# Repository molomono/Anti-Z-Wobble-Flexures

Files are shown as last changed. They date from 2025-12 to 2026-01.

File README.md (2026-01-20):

# Anti-Z-Wobble Flexures
Low cost SOTA performance 3d printable flexure based drop-in substitute for Oldham couplings.   
Onshape project focussing on solving z-axis misalignment and wobble induced printing artifacts using flexures.

---
Z-wobble in 3D printing is a mechanical issue where the Z-axis (vertical) movement isn't perfectly straight, 
causing the nozzle to shift slightly sideways, resulting in visible, repeating horizontal lines or ripples 
(Z-banding) on the print's surface. It's a hardware problem, often from bent lead screws, misaligned couplers,
and leads to inconsistent layer stacking. 

The approach to solving z-wobble and related artifacts is by releasing the x and y degrees of freedom at 
the interface between the T8-nut and the printer bed. (Same as any anti-wobble nut, oldham couplings, WobbleX) 
These DOFs are over-constrained by the linear rails AND the threaded rod. 
This project utilizes [Flexures](https://en.wikipedia.org/wiki/Flexure) to achieve this constraint relaxation. 
See [FACT](https://en.wikipedia.org/wiki/Freedom_and_constraint_topologies) for more info on design considerations.

---
## Quick Overview

Two primary designs, sharing common metrics for performance.   
	- High relative stiffness between z and x-y axes,    
		- High stiffness in z axis. Flexure must easily support the bed under fast accelrations.   
		- Low stiffness in x y axes.   
	- High resistance to tortion around z.   
	- Parametric Design So the dimensions of the model can easily be changed to better fit the users requirements. (see Onshape Workflow below)

Main benefits:   
	- Fixes minor misalignments, (releasing overconstrained Z-motion system)   
	- Flexure, thus no friction motion, therefore low hysteresis. (State of the Art performance for T8 threaded z-axis printers)   
	- Exceptionally low cost, (3D printed designs, practically free except for a few M2.5/M3 screws)   

Main downside:
	- Use in heated environments will require apropriate choice of material.

---

| Design | Key property | Onshape Link |
| :--- | :--- | :--- |
| **Design A V2: [Parallelogram]** | [Low x,y stiffness] | [Open Live Model 🔗](https://cad.onshape.com/documents/e9f5f3ec017cd79d059d23d6/w/ac5a599820a5beecc4798aae/e/dd3290a3d811bc061c931160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) |
| **Design A V3: [Parallelogram]** | [Stiffer Z DoFs] | [Open Live Model 🔗](https://cad.onshape.com/documents/0bdb8cc5919d48aaf7c68062/w/57636940a288332a187afe87/e/9ee4d49a4399172ee17dd28a) |
| **Design B: [Planar]** | [Flat profile] | [Open Live Model 🔗](https://cad.onshape.com/documents/95f8fcc605a67b3147b08d67/w/e3557ddfdb1231eb4b031d51/e/2aff83f88191c0ca42ad76a6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) |

---

## 1. Design A: [Parallelogram]
[V3 is the Recommended Design, well suited for 3d printing and dimensions are similar to oldham coupling.]

<p align="center">
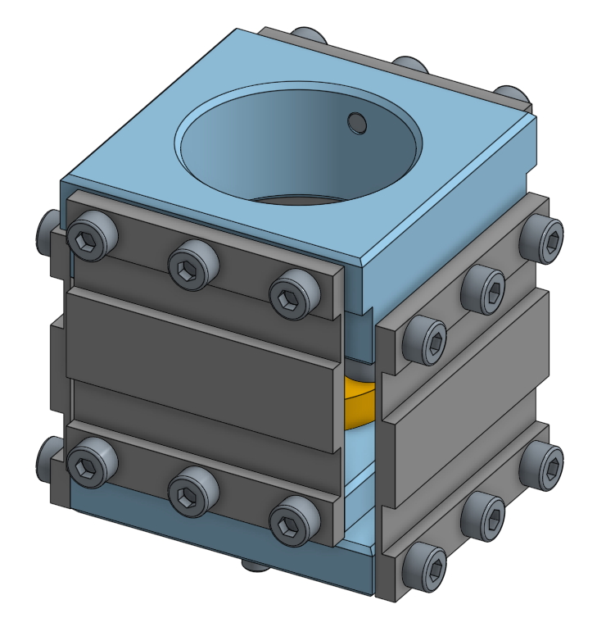
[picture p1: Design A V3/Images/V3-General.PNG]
  
</p>

<table border="0" align="center">
  <tr>
    <td>
      <p align="center"><b>Design A: Standard</b></p>
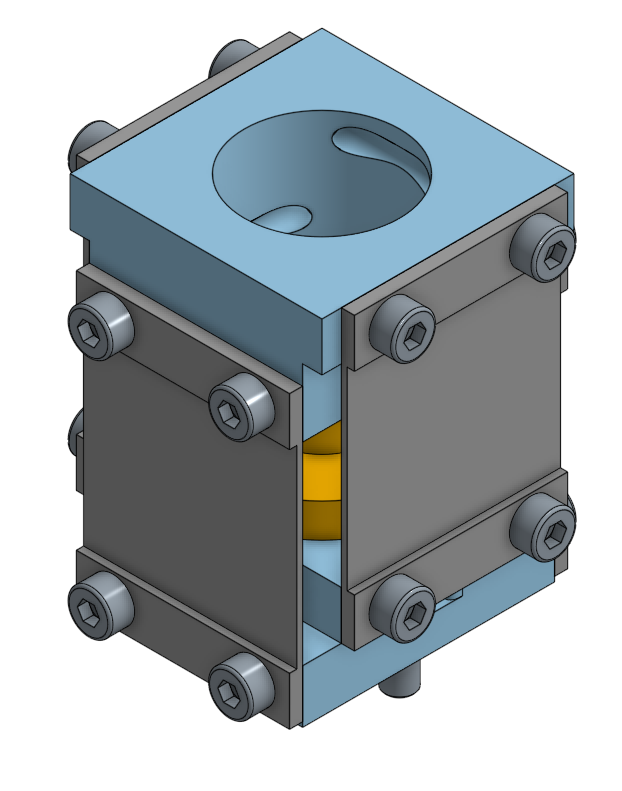
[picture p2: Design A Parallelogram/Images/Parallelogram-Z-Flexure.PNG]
      
    </td>
    <td>
      <p align="center"><b>Design A: Reinforced Leaf Springs</b></p>
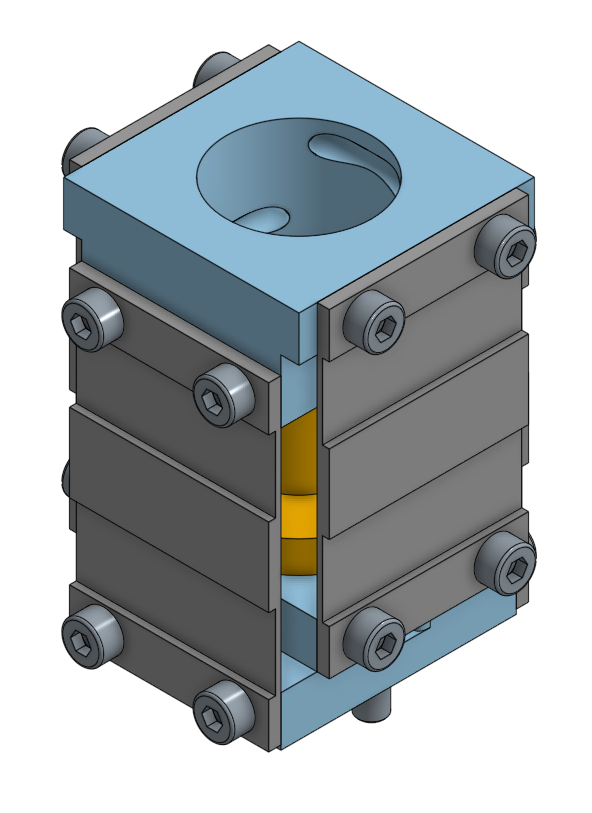
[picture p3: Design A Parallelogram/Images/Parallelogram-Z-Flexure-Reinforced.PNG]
      
    </td>
  </tr>
</table>

### Key Specifications
* **Standard Dimensions:** 28.7x28.7x37.5mm (without bolts)
* **Reinforced Dimensions:** 28.7x28.7x42.833mm (without bolts) (reinforced leaf spring version)
* **V3 Dimensions:** 38.8x38.8x39.0mm (without bolts) (V3 reinforced leaf spring version)
* **Hardware Required:** BOM: M3x8mm 8 times, M2.5x8mm 16 times (V3 uses 24), Threaded T8-Nut
* **Main Features:**  
	**Pros**: Easily achieves low x-y stiffness while maintaining high stiffness in other DOFs. 
		Easier printing, and stiffness tuning than design B.   
	**Cons**: Z-deflection becomes relational to x-y deflections (see figure) & "Tricky" assembly

<p align="center">
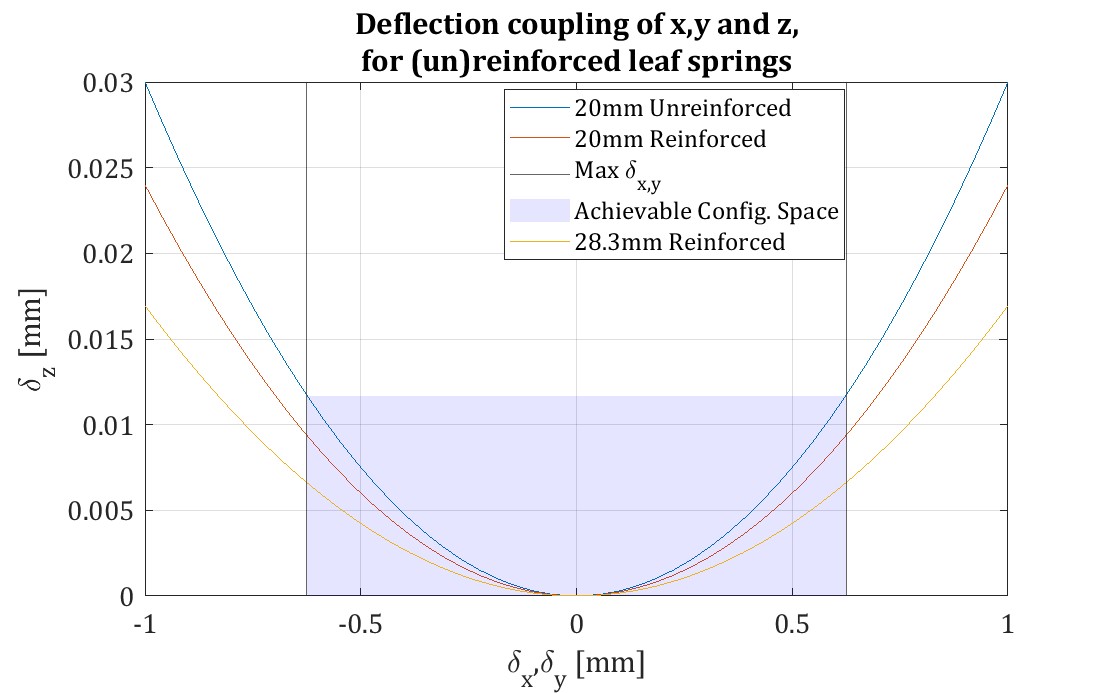
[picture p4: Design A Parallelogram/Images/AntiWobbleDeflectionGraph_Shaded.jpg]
Deflection in Z as product of deflection in x,y
  
</p>

<table border="0" align="center">
  <tr>
    <td>
      <p align="center"><b>Design A: Standard</b></p>
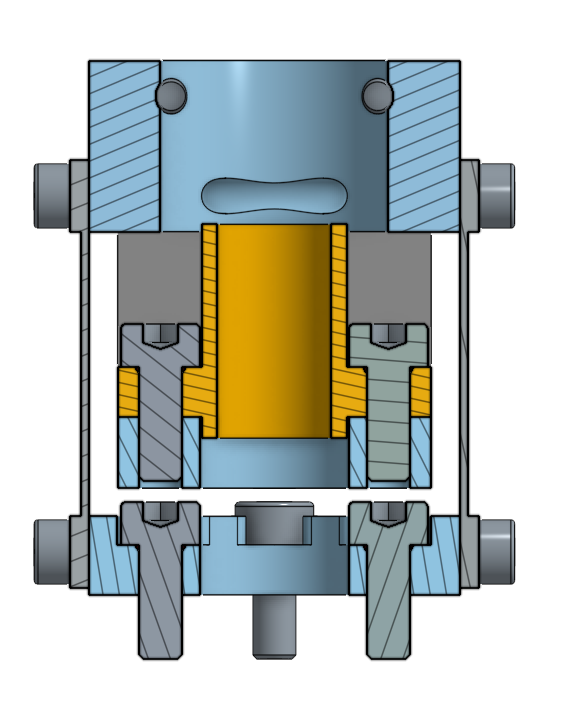
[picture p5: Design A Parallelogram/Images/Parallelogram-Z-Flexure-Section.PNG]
      
    </td>
    <td>
      <p align="center"><b>Design A: Reinforced Leaf Springs</b></p>
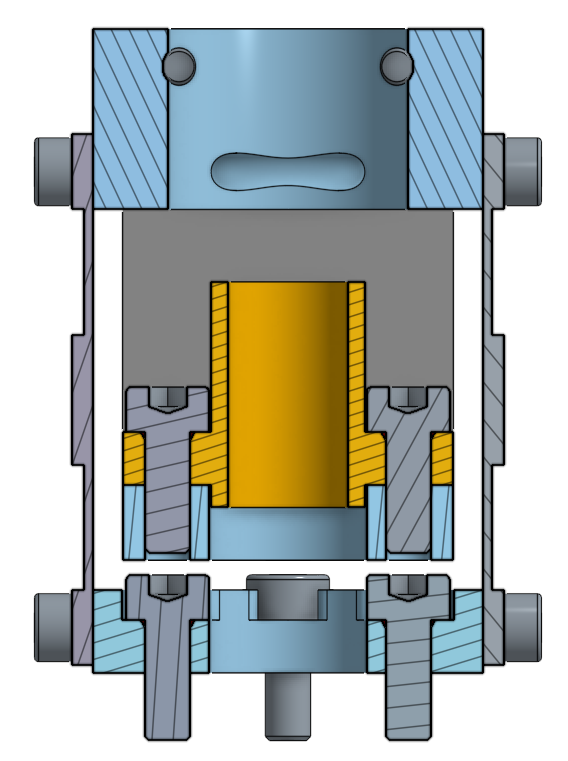
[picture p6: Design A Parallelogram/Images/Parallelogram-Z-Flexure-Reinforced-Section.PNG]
      
    </td>
  </tr>
</table>

**Note: Highly recommended to use Torx for any bolts below M3 because hex-bolts start stripping easily.**

---

## 2. Design B: [Planar]
[Experimentation with linear planar motion stages. This design works but is more difficult to print, but the design is well suited to be adapted for a CNC based solution can easily be machined.]

<p align="center">
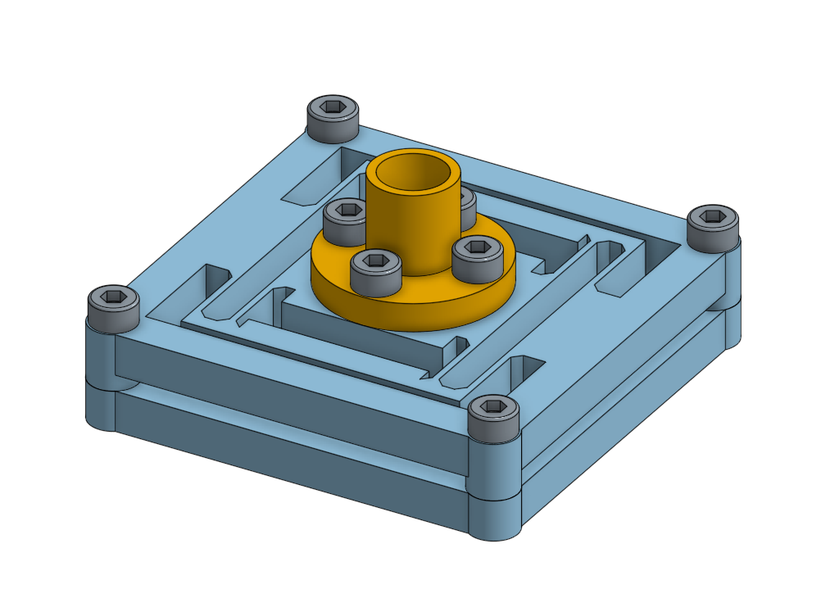
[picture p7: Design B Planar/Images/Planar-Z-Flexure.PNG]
  
</p>

### Key Specifications
* **Dimensions:** 52x52x12.5mm (without bolts)  
* **Hardware Required:** M3x8mm 8 times, M3x12mm 4 times, Threaded T8-Nut   
* **Main Features:**   
  	**Pros**: Very simple, symetric design, design structure well suited CNC machining.  
	**Cons**: Lower relative stiffness, akward shape, harder to print.  

<p align="center">
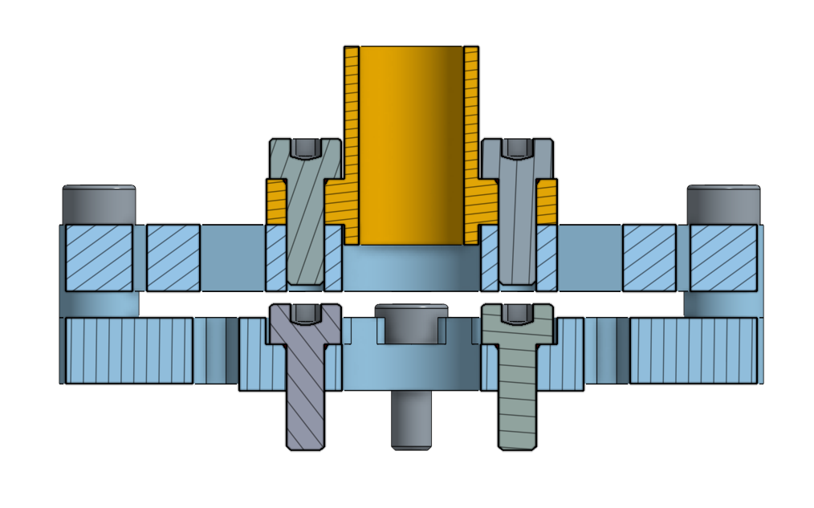
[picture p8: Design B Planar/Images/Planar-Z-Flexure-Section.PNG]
  
</p>

---

## Notes on print-settings
### Design A:
* I used PLA but PLA-CF/-GF might improve performance due to the print orietnation of the springs.
* Leaf springs must be printed flat with the reinforcements pointed up. Make sure that the unreinforced part of the springs is 100% considered bottom/top shell.
* Using rectilinear infill makes for good internal reinforcement structure. 30% is sufficient.
* Use 3-4 perimeter walls and 30% infill on the other printed boddies.
* Over-extruding the first layer is fine for functionality of this part, underextruding WILL cause issues.

### Design B:
* Make sure the seams do not align near the connection point between spring and body.
* Make sure the nozzle diameter ensures there are at least 2 walls in each spring.
* If the above requirements aren't met the springs can disconnect from the body.

---

### Onshape Workflow
To modify this design:
1. Open [Parallelogram Design](https://cad.onshape.com/documents/e9f5f3ec017cd79d059d23d6/w/ac5a599820a5beecc4798aae/e/dd3290a3d811bc061c931160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) or [Planar Design](https://cad.onshape.com/documents/95f8fcc605a67b3147b08d67/w/e3557ddfdb1231eb4b031d51/e/2aff83f88191c0ca42ad76a6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).
2. Click **"Make a Copy"** (requires a free Onshape account) to edit.
3. The variable table can be opened on the right from which dimensions of the model can be altered to better suit your needs.

---

## ⚖️ License

This project is licensed under the **Open Community License (OCL)**.
[View the full OCL terms here](https://github.com/OpenCommunityLicence/OpenCommunityLicence)

---

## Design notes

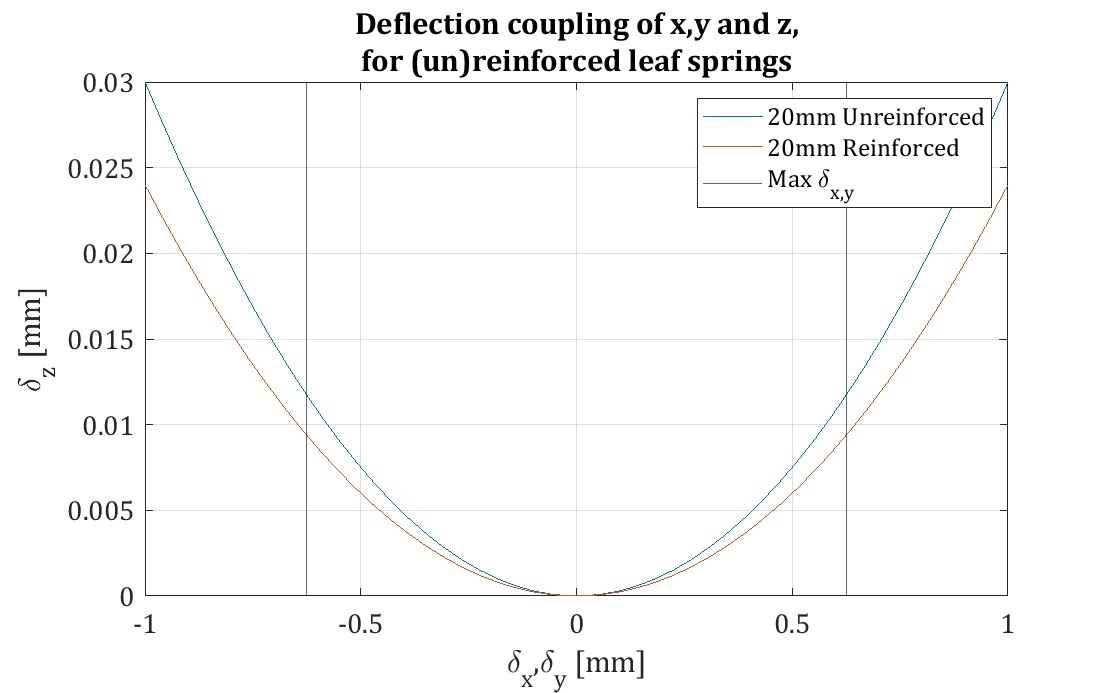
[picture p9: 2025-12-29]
Design A Parallelogram/Images/AntiWobbleDeflectionGraph.jpg

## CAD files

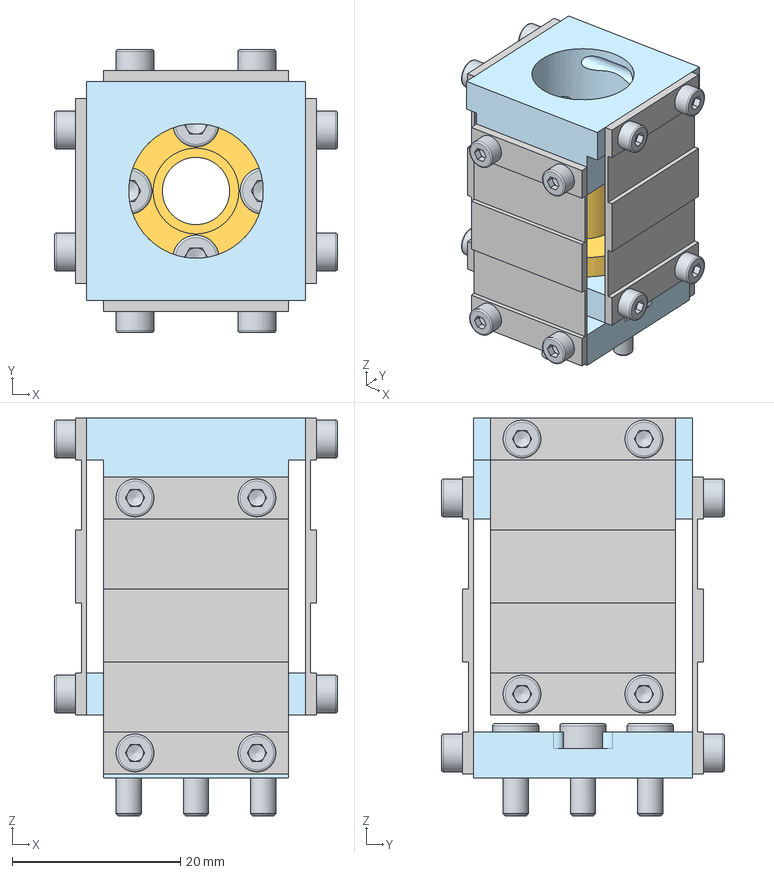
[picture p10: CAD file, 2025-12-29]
Design A Parallelogram/3D/CAD/Anti-Wobble-Flexure-M2.5 Reinforced.step
33.7 x 33.7 x 47.3 mm
Carriage Y
Hex socket head cap screw M3x0.50 x 8 x 8
Leaf1 x 4
Hex socket head cap screw M2.5x0.45 x 8 x 16
T8-Nut
Intermediate
Carriage X

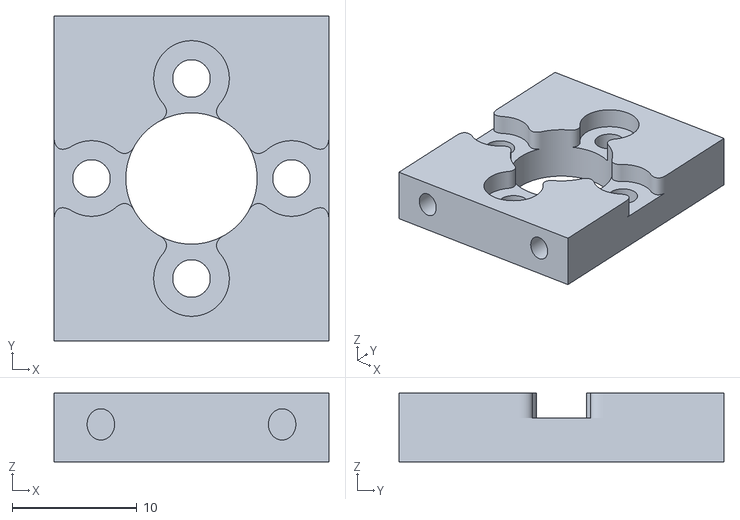
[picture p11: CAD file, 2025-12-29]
Design A Parallelogram/3D/WobbleFlexureM2.5 V2 - Carriage Bed.stl
22.0 x 26.0 x 5.50

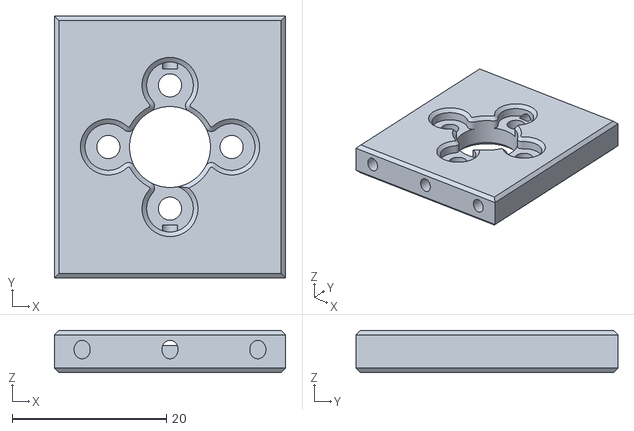
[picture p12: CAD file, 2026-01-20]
Design A V3/3D/WobbleFlexureM2.5 V3 - Carriage X.stl
30.0 x 34.0 x 5.50

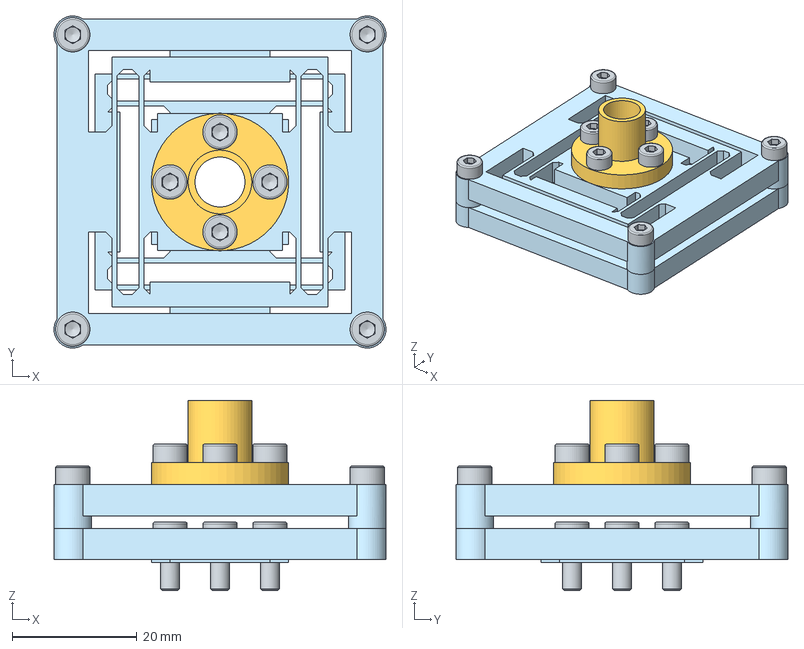
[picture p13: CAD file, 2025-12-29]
Design B Planar/3D/CAD/Anti-Wobble-Flexure-Planar.step
53.2 x 53.2 x 30.5 mm
Hex socket head cap screw M3x0.50 x 12 x 4
Carriage Top
Hex socket head cap screw M3x0.50 x 8 x 8
T8-Nut
Carriage Bottom

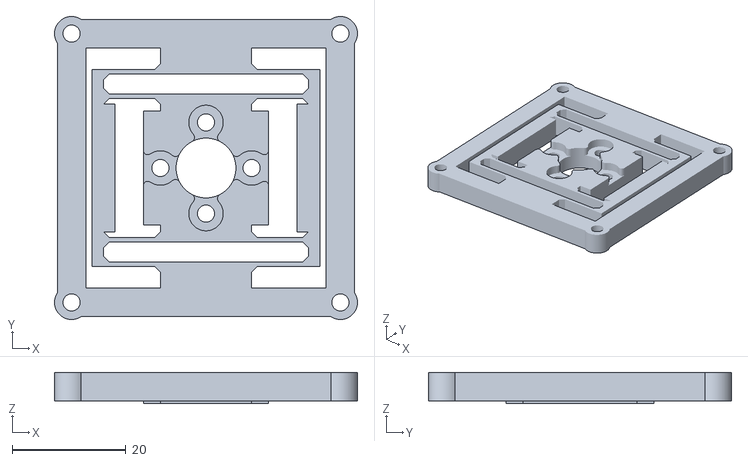
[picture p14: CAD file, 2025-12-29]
Design B Planar/3D/Wobble_Flexure_Planar - Carriage Bottom.stl
53.2 x 53.2 x 5.50

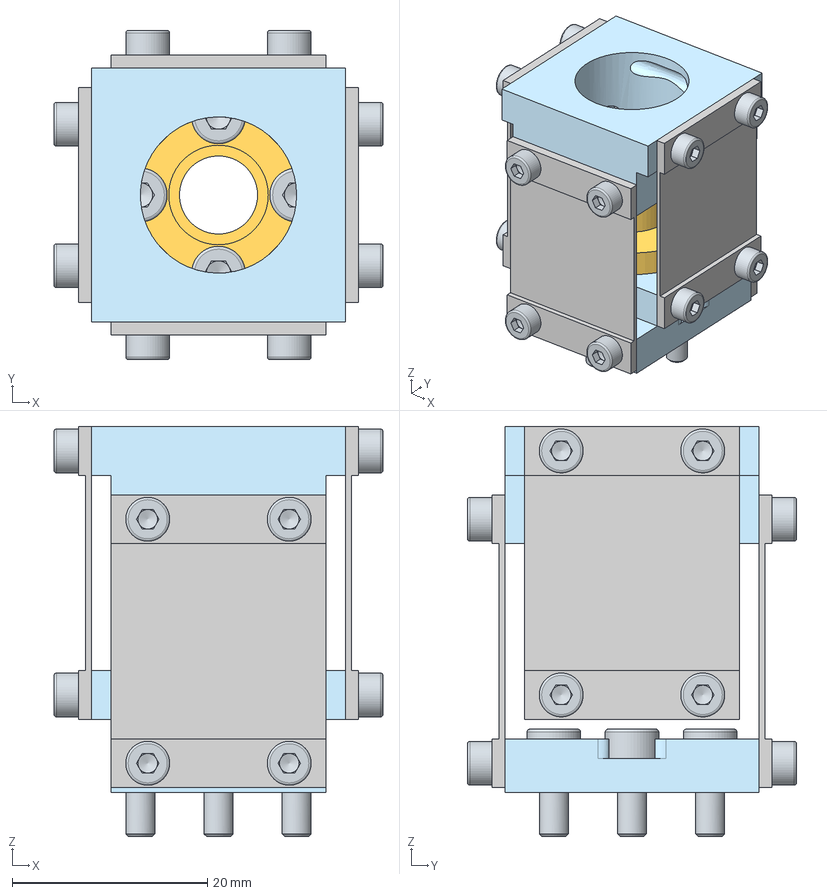
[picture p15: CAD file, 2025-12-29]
Design A Parallelogram/3D/CAD/Anti-Wobble-Flexure-M2.5 Short.step
33.7 x 33.7 x 42.0 mm
Carriage Y
Hex socket head cap screw M3x0.50 x 8 x 8
Leaf_Small x 4
Hex socket head cap screw M2.5x0.45 x 8 x 16
T8-Nut
Intermediate
Carriage X

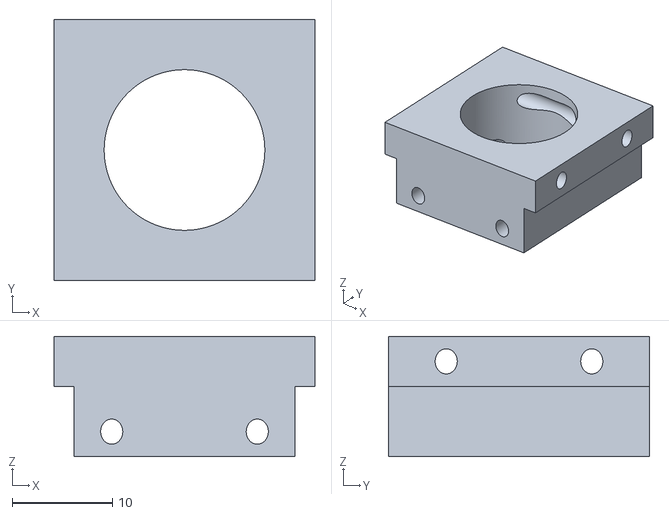
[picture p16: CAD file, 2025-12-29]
Design A Parallelogram/3D/WobbleFlexureM2.5 V2 - Intermediate.stl
26.0 x 26.0 x 12.0

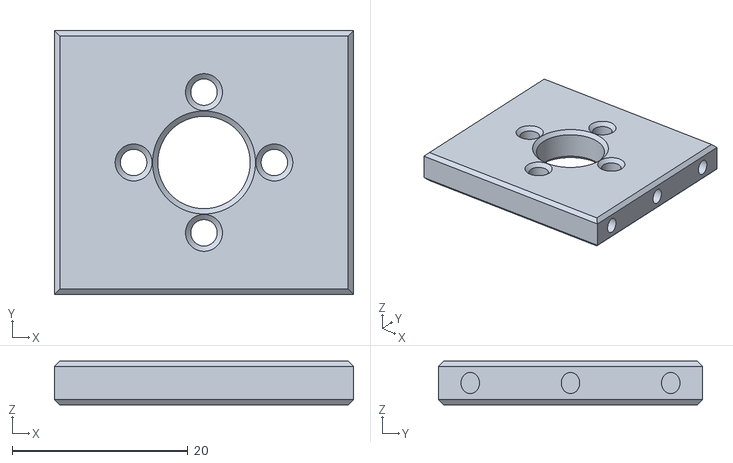
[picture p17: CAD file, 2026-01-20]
Design A V3/3D/WobbleFlexureM2.5 V3 - Carriage Y.stl
34.0 x 30.0 x 5.00

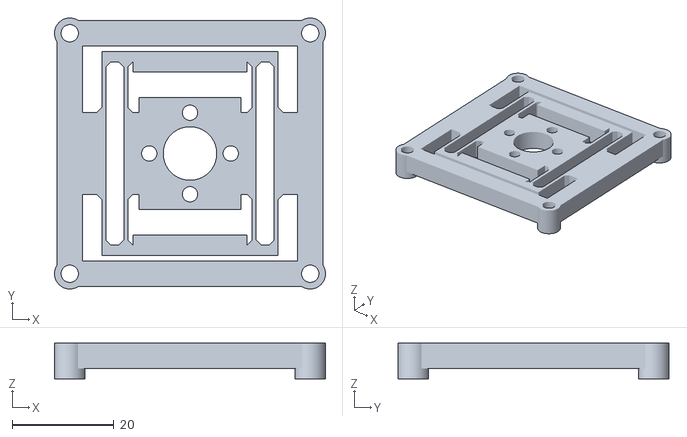
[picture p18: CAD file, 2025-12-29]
Design B Planar/3D/Wobble_Flexure_Planar - Carriage Top.stl
53.2 x 53.2 x 7.00

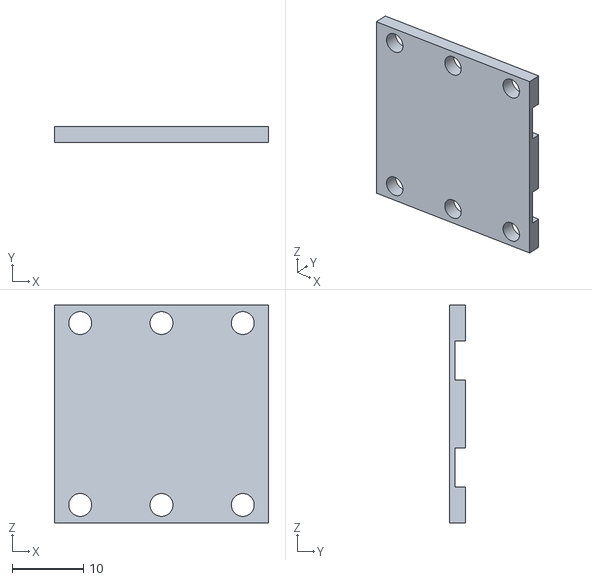
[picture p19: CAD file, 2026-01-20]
Design A V3/3D/WobbleFlexureM2.5 V3 - Leaf1 Reinforced.stl
30.0 x 2.25 x 30.5

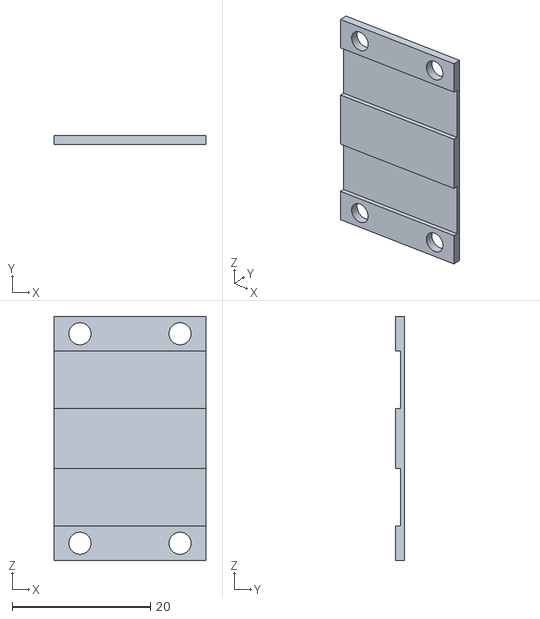
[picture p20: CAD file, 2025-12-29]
Design A Parallelogram/3D/WobbleFlexureM2.5 V2 - Leaf_Reinforced.stl
22.0 x 1.35 x 35.3

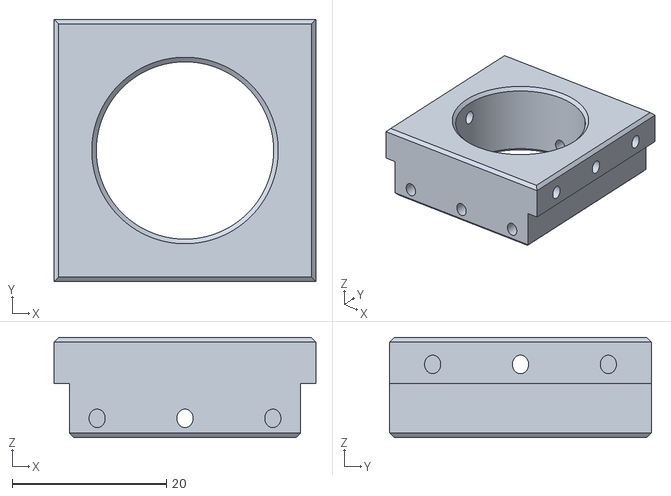
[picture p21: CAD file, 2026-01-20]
Design A V3/3D/WobbleFlexureM2.5 V3 - Intermediate.stl
34.0 x 34.0 x 13.0

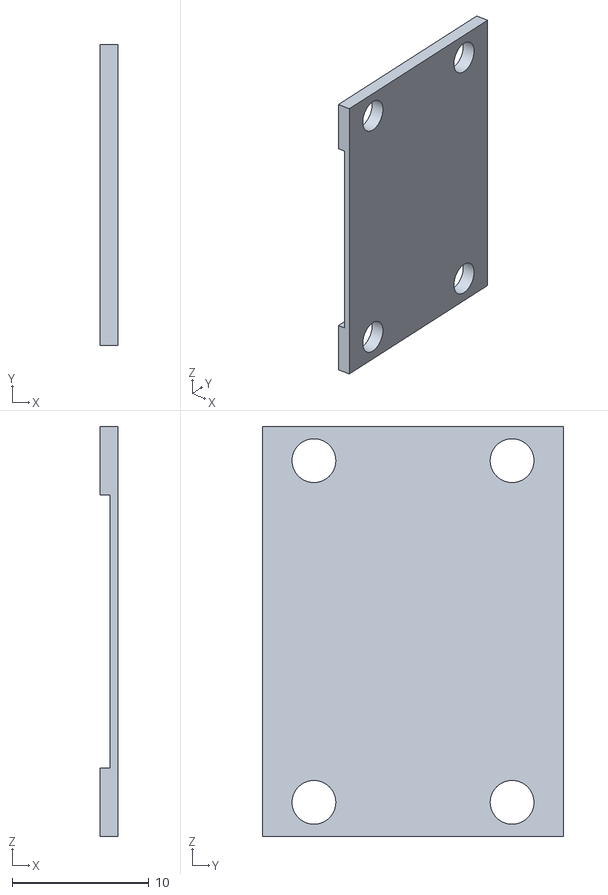
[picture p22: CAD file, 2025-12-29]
Design A Parallelogram/3D/WobbleFlexureM2.5 V2 - Leaf_Small.stl
1.35 x 22.0 x 30.0

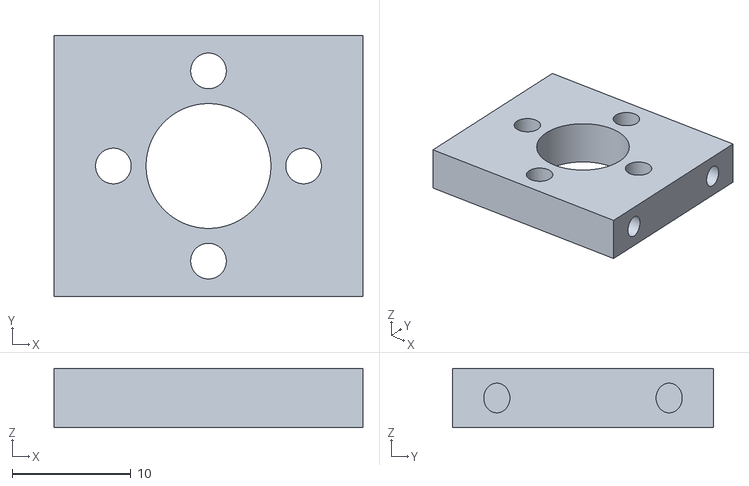
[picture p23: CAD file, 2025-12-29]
Design A Parallelogram/3D/WobbleFlexureM2.5 V2 - Carriage T-nut.stl
26.0 x 22.0 x 5.00

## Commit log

2025-12-29 Revise README with project details and specifications
    Updated project description and added details on Z-wobble issues in 3D printing. Expanded on design specifications and manufacturing instructions.
2025-12-29 Fix typo in README regarding heated environments
2026-01-20 adding V3
    [WobbleFlexureM2.5 V3 - Carriage X.stl, WobbleFlexureM2.5 V3 - Carriage Y.stl, WobbleFlexureM2.5 V3 - Intermediate.stl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]
2026-01-20 Update README with print settings notes
    Added notes on print settings for Design A and B.
